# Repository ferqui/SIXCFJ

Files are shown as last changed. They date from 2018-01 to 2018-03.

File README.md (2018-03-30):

# PROJECT SIXCFJ

## Table of Contents
1. [Description](#description)
2. [Requirements](#requirements)
3. [Software Requirements](#software-requirements)
4. [Installation](#installation)
5. [Connections](#connections)
6. [Android/iOS App](#androidios-application)
6. [Mentions](#mentions)
7. [Authors](#credits)

## Description
The objective was the creation of a maze solver using an Arduino Leonardo and some additional sensors. Moreover, once the robot has find the exit, it has to go back to the initial box using the minimal number of steps.

<p align="center">
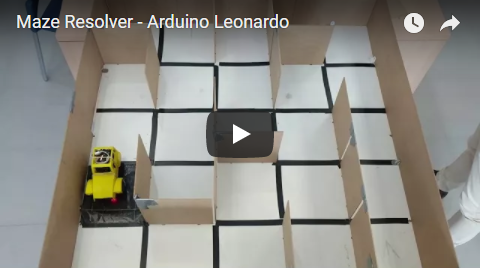
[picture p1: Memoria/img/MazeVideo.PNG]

</p>

## Requirements
* 1 Arduino Leonardo
* 1 Ultrasonic Sensor
* 2 Sharp Infrared Sensor
* 1 Bluetooth Module
* 2 Wheel
* 1 Motor driver
* 2 DC Motors
* 3 CNY70
* 3 LED RGB

## Software Requirements
* Arduino IDE
* React-Native

## Installation
First,

> git clone https://github.com/sixcfj/SIXCFJ.git

Once you have the repo, create a new Arduino project with the codes that are in *Arduino Codes/main*.  Then, you just need to upload it to your Arduino Leonardo and that's all.

## Connections

Pin  | Conection
-----| -----
A0 | CNY70 (Left)
A1 | CNY70 (Right)
A3 | Ultrasonic Sensor
A4 | Sharp Sensor (Right)
A5 | CNY70  (Back)
A6  | % of remaining Battery
A8 | Sharp Sensor (Left)
11 | LED3
12 | LED1
13 | LED2
RX,TX | Bluetooth

## Slides
In the slides directory you can run:

> npm start

This will runs the app in the development mode. Open http://localhost:3000 to view it in the browser.

## Android/iOS Application
First of all, download the dependencies with

> npm start

Then, you need to edit */node_modules/react-native-bluetooth-serial/android/src/main/java/com/rusel/RCTBluetoothSerial/RCTBluetoothSerialPackage* and delete those *__override__*.

Finally, just run one of these commands

> react-native run-android

> react-native run-ios

<p align="center">
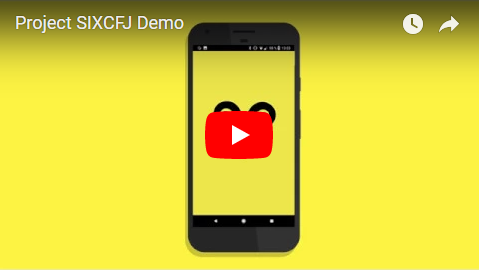
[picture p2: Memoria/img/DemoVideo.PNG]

</p>

About the songs, we can't share them due to copyright issues, but we encourage you to test it with your own music.

## Mentions
We would like to thanks maniacbug for creating this library, it was really helpful for our project. https://github.com/maniacbug/StandardCplusplus .

## Credits
  - Juan Francisco Cabrera Sánchez ([juanfrancs](https://github.com/juanfrancs))
  - Carlos Gallardo Polanco ([gpcarlos](https://github.com/gpcarlos))
  - Fernando Manuel Quintana Velazquez ([ferqui](https://github.com/ferqui))

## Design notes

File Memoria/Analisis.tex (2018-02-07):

\chapter{ANÁLISIS}
\vspace{-20pt}
\section{Casos de uso}

\scalebox{0.8}{
\begin{tikzpicture}
\begin{umlsystem}{Aplicación}
    \umlusecase[x=-3]{Visualizar información}
    \umlusecase[x=0, y=-1]{Conectarse}
    \umlusecase[x=-3,y=-3]{Manejar radiocontrol}
    \umlusecase[x=3,y=-3]{Seleccionar inicio}
\end{umlsystem}

\umlactor[x=-8]{Usuario}
\umlactor[x=8]{Robot}

\umlassoc{Usuario}{usecase-1}
\umlassoc{Usuario}{usecase-2}
\umlassoc{Usuario}{usecase-4}
\umlassoc{Robot}{usecase-2}
\umlassoc{Usuario}{usecase-3}

\end{tikzpicture}
}

\section{Diagrama de flujo}

\begin{figure}[h!]
\centering
\scalebox{0.8}{

\begin{tikzpicture}[node distance=2cm]
  \node (inicio) [startstop] {Inicio};
  \node (detect) [process,below of=inicio] {Detección};
  \node (dcha) [decision,below of=detect,yshift=-0.5cm,xshift=-6.5cm] {\footnotesize ¿Mov Derecha?};
  \node (front) [decision,right of=dcha,xshift=2cm] {\footnotesize ¿Mov Frente?};
  \node (izqda) [decision,right of=front,xshift=2cm] {\footnotesize ¿Mov Izquierda?};
  \node (movDerecha) [process,below of=dcha,yshift=-1cm] {Mov Derecha};
  \node (movFrente) [process,below of=front,yshift=-1cm] {Mov Frente};
  \node (movIzquierda) [process,below of=izqda,yshift=-1cm] {Mov Izquierda};
  \node (movAtras) [process,right of=movIzquierda,xshift=2.5cm] {Deshacer movimiento};
  \node (final) [decision,below of=movFrente,yshift=-1cm,xshift=2cm] {\footnotesize ¿Casilla final?};
  \node (Inv) [process,below of=final,yshift=-1cm] {Camino Inverso};
  \node (null) [right of= movAtras]{\ };

  \draw[arrow] (inicio) -- (detect);
  \draw[arrow] (detect) -| (dcha);
  \draw[arrow] (dcha) -- node[anchor=south]{No} (front);
  \draw[arrow] (front) -- node[anchor=south]{No} (izqda);
  \draw[arrow] (dcha) -- node[anchor=west]{Sí} (movDerecha);
  \draw[arrow] (izqda) -- node[anchor=west]{Sí} (movIzquierda);
  \draw[arrow] (front) -- node[anchor=west]{Sí} (movFrente);
  \draw[arrow] (izqda) -| node[anchor=south]{No}(movAtras);
  \draw[arrow] (movDerecha) -- node[anchor=west]{}(final);
  \draw[arrow] (movIzquierda) -- node[anchor=west]{}(final);
  \draw[arrow] (movFrente) -- node[anchor=west]{}(final);
  \draw[arrow] (movAtras) -- node[anchor=west]{}(final);
  \draw (final.east) -| node[anchor=west]{No} (null.north);
  \draw[arrow] (null) |- (detect.east);
  \draw[arrow] (final) -- node[anchor=west]{Sí}(Inv);
  %\draw[arrow] (final) to[out=-230,in=150] node[anchor=south]{No}(detect);
\end{tikzpicture}
}
\caption{Diagrama de flujo}
\end{figure}

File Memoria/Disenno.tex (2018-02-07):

\chapter{DISEÑO}

\section{Estructura}

Seguidamente puede ver el código principal para la resolucón del laberinto:

\inputminted{arduino}{code/main.ino}

\vspace{-15pt}
\section{Plan de pruebas}
Se ha implementado una pequeña función que nos permite, a partir mediante Bluetooth conocer el estado de los sensores y poder actuar en consecuencia si las mediciones son anormales.

\begin{minted}{cpp}
void testSensors() {
  if (robot.ReadCNY('L'))
    Serial1.println("CNY L Black");
  else
    Serial1.println("CNY L White");
  if (robot.ReadCNY('R'))
    Serial1.println("CNY R Black");
  else
    Serial1.println("CNY R White");
  if (robot.ReadCNY('B'))
    Serial1.println("CNY B Black");
  else
    Serial1.println("CNY B White");
  Serial1.print("Ultrasonic: "); Serial1.println(robot.ReadUltrasonic());
  Serial1.print("Sharp L: "); Serial1.println(robot.ReadSharp('L'));
  Serial1.print("Sharp R: "); Serial1.println(robot.ReadSharp('R'));
}
\end{minted}

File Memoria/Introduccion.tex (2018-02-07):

\chapter{INTRODUCCIÓN}

\section{Objetivo}
El objetivo de esta práctica es la resolución de un laberinto de 5x5 casillas, en el que la posición de las paredes, se desconoce a priori y en el que las casillas tienen un tamaño de 20x20 cm. Además de resolver el laberinto, es decir, llegar a una casilla de salida cuya posición se desconoce. Una vez que se haya encontrado la casilla de salida, volver a la casilla de entrada por el camino más corto posible.

\begin{itemize}
  \item Movimientos: Desplazamiento hacia delante, hacia atrás, giro a la izquierda y giro a la derecha
  \item Detección: Detección de paredes mediante el uso de sensores Sharp y ultrasonidos, y detección de color mediante el uso de sensores CNY70.
  \item Recogida de información: Se recoge información desde los sensores Sharp, CNY70 y el ultrasonidos.
  \item Algoritmo de resolución del laberinto: Se tiene una jerarquía de movimientos, estando en primer lugar, moverse a la derecha, luego al frente y por último a la izquierda. Todos estos movimientos se van guardando en una pila para que según se vaya avanzando en el laberinto en la pila sólo queden los movimientos que permiten alcanzar la casilla final, para que haciendo los movimientos inversos a los que están en la pila, el robot pueda volver a llegar a la casilla inicial por el camino más corto.
  \item Monitorización de información: La monitorización de la información se realiza a través de la aplicación móvil, que muestra la posición del robot en el laberinto junto con el nivel de batería restante, entre otras cosas.

\end{itemize}

\section{Hardware empleado}
En el diseño final se han utilizado los siguientes componentes:

\begin{itemize}
  \item CNY70: Sensor que mide la intensidad de la luz, permitiendo distinguir colores.
  \item Ultrasonidos: Sensor que permite calcular distancias mediante la producción de sonidos y su rebote.
  \item Sharp: Sensor que permite calcular las distancias mediante el uso de un haz de luz.
  \item HC-06 (Bluetooth): Módulo que permite leer y escribir datos mediante el puerto serie.
  \item Motores DC: Elemento mecánico que permite el movimiento.
  \item LED: Elemento electrónico que se ilumina con el paso de la corriente.
  \item Batería: Proporciona una fuente de alimentación externa.
\end{itemize}

\subsection{Arduino Leonardo}

Para ello, se utilizará una placa Arduino Leonardo, un ordenador personal y un móvil. A través del ordenador, se le descargará en la placa el programa para resolver el laberinto, una vez realizada la descarga del programa, se enlaza mediante Bluetooth la placa y un dispositivo móvil, donde se podrá ver la posición del robot en el laberinto y otros datos interesantes como el porcentaje de batería restante.

\subsection{Sensores}
\begin{itemize}
  \item CNY70: Su uso es necesario para comprobar el paso de una casilla a otra así como para comprobar si se ha llegado a la casilla de salida o no.
  \item Sharp: Se usa para detectar la existencia de paredes laterales.
  \item Ultrasonidos: Se usa para detectar la existencia de paredes frontales.
\end{itemize}

\subsection{Actuadores}
\begin{itemize}
  \item Interruptor: El interruptor es necesario para encender la placa.
\end{itemize}

\subsection{Elementos de comunicación}
\begin{itemize}
  \item HC-06: El conector Bluetooth se usa para mandar información a la app móvil para que en ésta se vean el nivel batería y la posición en el laberinto.
\end{itemize}

\subsection{Alimentación}
\begin{itemize}
  \item Batería de 6 pilas AA: Sirve para alimentar la placa.
\end{itemize}

\subsection{Justificación}
Se consideran que estos elementos son los mínimos imprescindibles para una correcta resolución del laberinto, ya que, desde un primer momento, el hecho de buscar un diseño similar al de un coche, teníamos claro que el ultrasonidos iría colocado en el lugar de los faros delanteros y por lo tanto, el uso de los servos resulta totalmente prescindible. Por otra parte, tampoco se usa el conector Bluetooth para el PC por estar utilizando una aplicación móvil.

\subsection{Resumen de Pines}
\begin{table}[h!]
  \centering
  \begin{tabular}{cc}

      \begin{tabular}{|c|c|}
        \hline
        PIN & ELEMENTO \\ \hline
        A5 & CNY Trasero \\ \hline
        A0 & CNY Izquierdo \\ \hline
        A1 & CNY Derecho \\ \hline
        A8 & Sharp Izquierdo \\ \hline
        A4 & Sharp Derecho \\ \hline
        RX, TX & Bluetooth \\ \hline
        A3 & Ultrasonidos \\ \hline
        12 & LED1 \\ \hline
        13 & LED2 \\ \hline
        11 & LED3 \\ \hline
        A6 & \% Batería \\ \hline

      \end{tabular}
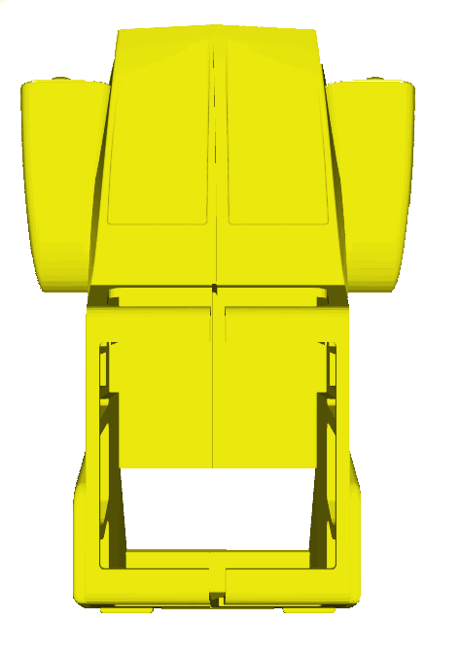
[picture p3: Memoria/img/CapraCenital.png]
    &  \vcenteredhbox{}\\
  \end{tabular}
  \caption{Resumen de los elementos y sus respectivos pines}
  \label{}
\end{table}

\section{Software empleado}
\subsection{Arduino IDE}
Resulta imprescindible el uso de este software por motivos obvios, gracias a él se le mandan los programas a la placa de Arduino. En nuestro caso, era también necesario para importar la librería externa que contiene la implementación de las estructuras de datos de la STL de C++ en Arduino, aunque ésto se detallará más adelante.

\subsection{React-Native}
\textit{React-Native} es una librería de Javascript que permite la creación de aplicaciones que tengan una apariencia nativa en el correspondiente sistema operativo móvil, en este caso en Android y iOS, usando un mismo código. ¿Por qué usar un móvil y no un PC? La respuesta viene dada con dos componentes, el primero la portabilidad y el segundo, la potencia.

Comenzando por la portabilidad, es evidente que es muchísimo más fácil transportar un móvil que un ordenador portátil, de esta forma, ante la posibilidad de tener que hacer presentaciones, sólo haría falta el robot y el móvil, ya que la placa de Arduino poseer una memoria flash, llevaría cargado el programa previamente. En cuanto a la potencia, la realidad es que en los últimos años la tecnología móvil ha avanzado lo suficiente como para igualar en ciertos aspectos al ordenador portátil, por tanto, si tuviesemos que mandar a realizar unos cálculos ya sea al ordenador o al móvil, como por ejemplo, calcular el camino de vuelta más corto usando el algoritmo de Dijkstra no habría tanta diferencia entre que lo haga un móvil o un ordenador.

Y, por otro lado, está el factor didáctico. \textit{React-Native} es una librería con un gran empuje en los últimos años y, de cara a aumentar nuestra formación en otras tecnologías, resultaba bastante interesante aprender lo más actual en el mundo empresarial.

\subsection{\LaTeX}
El hecho de utilizar \LaTeX \ era obligatorio en nuestra opinión para dotar a esta memoria de un aspecto académico, gracias en gran medida al paquete TikZ que permite la creación de gráficos vectoriales en \LaTeX \ con una gran versatilidad. Este paquete permite, por ejemplo, la creación de diagramas de Gantt, de diagramas de casos de uso o de diagramas de flujo.

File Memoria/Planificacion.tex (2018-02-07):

\chapter{PLANIFICACIÓN}

En la primera reunión se decidió que todos colaboraríamos en la codificación del algoritmo del robot y que, además, cada uno de los integrantes del grupo, además de esta tarea, abarcaría otra tarea individual. Esto queda claro en el sistema de colores empleado en diagrama de Gantt que podrá ver en la siguiente página.

\begin{landscape}
\makebox[15pt][c]{
\begin{minipage}{0.21\linewidth}
\begin{ganttchart}[
  hgrid,vgrid, x unit=2mm, time slot format=isodate,newline shortcut=true,
bar label node/.append style=%
{align=center},
bar label font={\footnotesize},
  x unit=0.32cm, canvas/.style={fill=yellow!10,draw=gray,very thick},
  title label font={\tiny}
]{2017-11-25}{2018-2-13}
  \gantttitlecalendar{year,month=name,day} \\
  \ganttbar[bar/.append style={fill=RedOrange!40}]{Códigos\\ sensores}{2017-11-25}{2017-11-30}\\
  \ganttlinkedbar[bar/.append style={fill=RedOrange!40}]{Librería}{2017-11-30}{2018-01-15}\\
  \ganttbar[bar/.append style={fill=Yellow!60}]{Diseño\\ piezas 3D}{2017-12-15}{2018-01-02}\\
  \ganttlinkedbar[bar/.append style={fill=Yellow!60}]{Impresión\\ piezas 3D}{2018-01-02}{2018-01-06}\\
  \ganttlinkedbar[bar/.append style={fill=RedOrange!40}]{Pruebas}{2018-01-06}{2018-01-10}\\
  \ganttlinkedbar[bar/.append style={fill=RedOrange!40}]{Implementación\\ del algoritmo}{2017-12-16}{2018-2-12}\\
  \ganttbar[bar/.append style={fill=LimeGreen!50}]{Aplicación\\móvil}{2017-12-10}{2018-02-12}\\
  \ganttbar[bar/.append style={fill=RoyalBlue!20}]{Documentación}{2017-11-25}{2018-02-06}
\end{ganttchart}
\end{minipage}
}

\

\begin{center}
\crule[LimeGreen!50]{0.5cm}{0.5cm} Fernando \hspace{1cm}
\crule[RoyalBlue!20]{0.5cm}{0.5cm} Juan Francisco \hspace{1cm}
\crule[Yellow!60]{0.5cm}{0.5cm} Carlos \hspace{1cm}
\crule[RedOrange!40]{0.5cm}{0.5cm} Común
\end{center}

\end{landscape}

\restoregeometry

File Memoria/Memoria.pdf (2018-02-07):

# Project SIXCFJ (Robot Móvil)

# https://github.com/ferqui/SIXCFJ

## Juan Francisco Cabrera Sánchez Carlos Gallardo Polanco Fernando Manuel Quintana Velázquez

## 7 de febrero de 2018

# Índice general

1. INTRODUCCIÓN | 5
2. ESPECIFICACIÓN DE REQUISITOS | 8
3. PLANIFICACIÓN | 9
4. PRESUPUESTO | 11
5. ANÁLISIS | 12

6. DISEÑO | 13
7. IMPLEMENTACIÓN | 16
8. MONTAJE | 17
9. PRUEBAS | 20
10. MEJORAS | 21
Apéndices | 22
A. Especificacion del TAD Robot | 23
B. Implementacion del TAD Robot | 24

# Índice de figuras

5.1. Diagrama de flujo | | 12
8.1. Elementos del robot | | 17
8.2. Diseño de las piezas 3D | | 17
8.3. Piezas del Ultrasonidos y los Sharp | | 18
8.4. Imagen del robot con su chásis | | 18
8.5. Galería del robot | | 19
8.6. Muestra de la aplicación móvil | | 19

# Índice de cuadros

# Capítulo 1

# INTRODUCCIÓN

## 1.1. Objetivo

El objetivo de esta práctica es la resolución de un laberinto de 5x5 casillas, en el que la posición de las paredes, se desconoce a priori y en el que las casillas tienen un tamaño de 20x20 cm. Además de resolver el laberinto, es decir, llegar a una casilla de salida cuya posición se desconoce. Una vez que se haya encontrado la casilla de salida, volver a la casilla de entrada por el camino más corto posible.

Movimientos: Desplazamiento hacia delante, hacia atrás, giro a la izquierda y giro a la derecha

Detección: Detección de paredes mediante el uso de sensores Sharp y ultrasonidos, y detección de color mediante el uso de sensores CNY70.

Recogida de información: Se recoge información desde los sensores Sharp, CNY70 y el ultrasonidos.

Algoritmo de resolución del laberinto: Se tiene una jerarquía de movimientos, estando en primer lugar, moverse a la derecha, luego al frente y por último a la izquierda. Todos estos movimientos se van guardando en una pila para que según se vaya avanzando en el laberinto en la pila sólo queden los movimientos que permiten alcanzar la casilla final, para que haciendo los movimientos inversos a los que están en la pila, el robot pueda volver a llegar a la casilla inicial por el camino más corto.

Monitorización de información: La monitorización de la información se realiza a través de la aplicación móvil, que muestra la posición del robot en el laberinto junto con el nivel de batería restante, entre otras cosas.

## 1.2. Hardware empleado

## En el diseño final se han utilizado los siguientes componentes:

CNY70: Sensor que mide la intensidad de la luz, permitiendo distinguir colores.

Ultrasonidos: Sensor que permite calcular distancias mediante la producción de sonidos y su rebote.

Sharp: Sensor que permite calcular las distancias mediante el uso de un haz de luz.

HC-06 (Bluetooth): Módulo que permite leer y escribir datos mediante el puerto serie.

Motores DC: Elemento mecánico que permite el movimiento.

LED: Elemento electrónico que se ilumina con el paso de la corriente.

Batería: Proporciona una fuente de alimentación externa.

## 1.2.1. Arduino Leonardo

Para ello, se utilizará una placa Arduino Leonardo, un ordenador personal y un móvil. A través del ordenador, se le descargará en la placa el programa para resolver el laberinto, una vez realizada la descarga del programa, se enlaza mediante Bluetooth la placa y un dispositivo móvil, donde se podrá ver la posición del robot en el laberinto y otros datos interesantes como el porcentaje de batería restante.

## 1.2.2. Sensores

CNY70: Su uso es necesario para comprobar el paso de una casilla a otra así como para comprobar si se ha llegado a la casilla de salida o no.

Sharp: Se usa para detectar la existencia de paredes laterales.

Ultrasonidos: Se usa para detectar la existencia de paredes frontales.

## 1.2.3. Actuadores

Interruptor: El interruptor es necesario para encender la placa.

## 1.2.4. Elementos de comunicación

HC-06: El conector Bluetooth se usa para mandar información a la app móvil para que en ésta se vean el nivel batería y la posición en el laberinto.

## 1.2.5. Alimentación

Batería de 6 pilas AA: Sirve para alimentar la placa.

## 1.2.6. Justificación

Se consideran que estos elementos son los mínimos imprescindibles para una correcta resolución del laberinto, ya que, desde un primer momento, el hecho de buscar un diseño similar al de un coche, teníamos claro que el ultrasonidos iría colocado en el lugar de los faros delanteros y por lo tanto, el uso de los servos resulta totalmente prescindible. Por otra parte, tampoco se usa el conector Bluetooth para el PC por estar utilizando una aplicación móvil.

## 1.2.7. Resumen de Pines

PIN | ELEMENTO

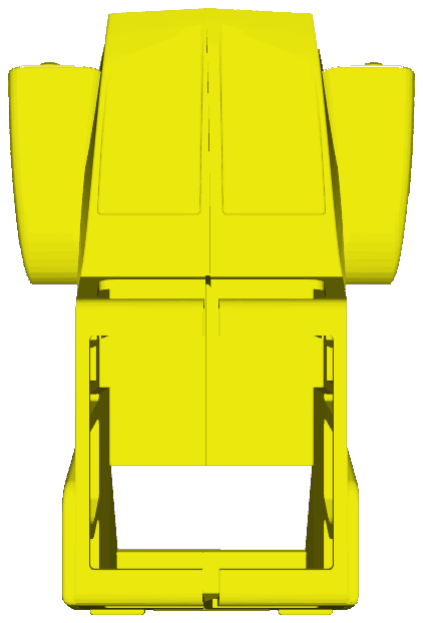
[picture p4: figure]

A5 | CNY Trasero
A0 | CNY Izquierdo
A1 | CNY Derecho
A8 | Sharp Izquierdo
A4 | Sharp Derecho
RX, TX | Bluetooth
A3 | Ultrasonidos
12 | LED1
13 | LED2
11 | LED3
A6 | % Batería

## Cuadro 1.1: Resumen de los elementos y sus respectivos pines

## 1.3. Software empleado

## 1.3.1. Arduino IDE

Resulta imprescindible el uso de este software por motivos obvios, gracias a él se le mandan los programas a la placa de Arduino. En nuestro caso, era también necesario para importar la librería externa que contiene la implementación de las estructuras de datos de la STL de C++ en Arduino, aunque ésto se detallará más adelante.

## 1.3.2. React-Native

React-Native es una librería de Javascript que permite la creación de aplicaciones que tengan una apariencia nativa en el correspondiente sistema operativo móvil, en este caso en Android y iOS, usando un mismo código. ¿Por qué usar un móvil y no un PC? La respuesta viene dada con dos componentes, el primero la portabilidad y el segundo, la potencia.
Comenzando por la portabilidad, es evidente que es muchísimo más fácil transportar un móvil que un ordenador portátil, de esta forma, ante la posibilidad de tener que hacer presentaciones, sólo haría falta el robot y el móvil, ya que la placa de Arduino poseer una memoria flash, llevaría cargado el programa previamente. En cuanto a la potencia, la realidad es que en los últimos años la tecnología móvil ha avanzado lo suficiente como para igualar en ciertos aspectos al ordenador portátil, por tanto, si tuviesemos que mandar a realizar unos cálculos ya sea al ordenador o al móvil, como por ejemplo, calcular el camino de vuelta más corto usando el algoritmo de Dijkstra no habría tanta diferencia entre que lo haga un móvil o un ordenador.
Y, por otro lado, está el factor didáctico. React-Native es una librería con un gran empuje en los últimos años y, de cara a aumentar nuestra formación en otras tecnologías, resultaba bastante interesante aprender lo más actual en el mundo empresarial.

## 1.3.3. LATEX

El hecho de utilizar LATEX era obligatorio en nuestra opinión para dotar a esta memoria de un aspecto académico, gracias en gran medida al paquete TikZ que permite la creación de gráficos vecto-riales en LATEX con una gran versatilidad. Este paquete permite, por ejemplo, la creación de diagramas de Gantt, de diagramas de casos de uso o de diagramas de flujo.

# Capítulo 2

# ESPECIFICACIÓN DE REQUISITOS

## 2.1. Requisitos funcionales

ID | CATEGORÍA | DESCRIPCIÓN
RF01 | Movimiento | El robot debe ser capaz de moverse
RF02 | Movimiento | El robot debe ser capaz de pivotar 90º a derecha
RF03 | Movimiento | El robot debe ser capaz de pivotar 90º a izquierda
RF04 | Movimiento | El robot debe ser capaz de avanzar en línea recta
RF05 | Movimiento | El robot avanza adecuadamente hasta la siguiente celda
RF06 | Detección | El robot debe ser capaz de detectar una pared frontal
RF07 | Detección | El robot debe ser capaz de detectar una pared lateral derecha
RF08 | Detección | El robot debe ser capaz de detectar una pared lateral izquierda
RF09 | Detección | El robot debe ser capaz de detectar la transición entre celdas
RF10 | Detección | El robot debe ser capaz de detectar la celda de salida
RF11 | Resolución | El robot almacena información sobre las celdas del laberinto
RF12 | Resolución | El robot es capaz de decidir el siguiente movimiento en base a la información sobre la celda
RF13 | Resolución | El robot es capaz de recorrer varias celdas del laberinto siguiendo el algoritmo empleado
RF14 | Resolución | El robot es capaz de salir del laberinto
RF15 | Información | El robot envía al PC información sobre el número de celdas recorridas
RF16 | Información | El robot envía al PC información sobre obstáculos en cada celda
RF17 | Información | El robot envía al PC información sobre la velocidad de movimiento
RF18 | Información | El robot envía al PC información sobre la distancia recorrida
RF19 | Información | El robot envía al PC información sobre el tiempo transcurrido desde la entrada al laberinto
RF20 | Información | El robot envía al PC sobre la trayectoria ejecutada
RF21 | Información | El robot envía al PC información sobre el número de celdas recorridas
RF22 | Información | El PC muestra una representación gráfica del laberinto
RF23 | Usuario | Interfaz gráfica en PC que recopile información
RF24 | Pruebas | Incluir modo test al arranque del robot

## Cuadro 2.1: Requisitos Funcionales

## 2.2. Requisitos no funcionales

ID | CATEGORÍA | DESCRIPCIÓN | ACCIÓN
RNF01 | Tamaño | Condicionado por las dimensiones del laberinto <Casilla de 20cm x 20cm; Laberinto de 1m x 1m>
RNF02 | Consumo | Condicionado por la batería disponible <6 pilas AA >
RNF03 | Errores | El robot choca contra una pared | -
RNF04 | Errores | Batería a punto de agotarse | Sustituir batería
RNF05 | Errores | El robot gira continuamente | No se produce
RNF06 | Errores | El robot sobrepasa 20 minutos sin conseguir salir | -

## Cuadro 2.2: Requisitos no Funcionales

# Capítulo 3

# PLANIFICACIÓN

En la primera reunión se decidió que todos colaboraríamos en la codificación del algoritmo del robot y que, además, cada uno de los integrantes del grupo, además de esta tarea, abarcaría otra tarea individual. Esto queda claro en el sistema de colores empleado en diagrama de Gantt que podrá ver en la siguiente página.

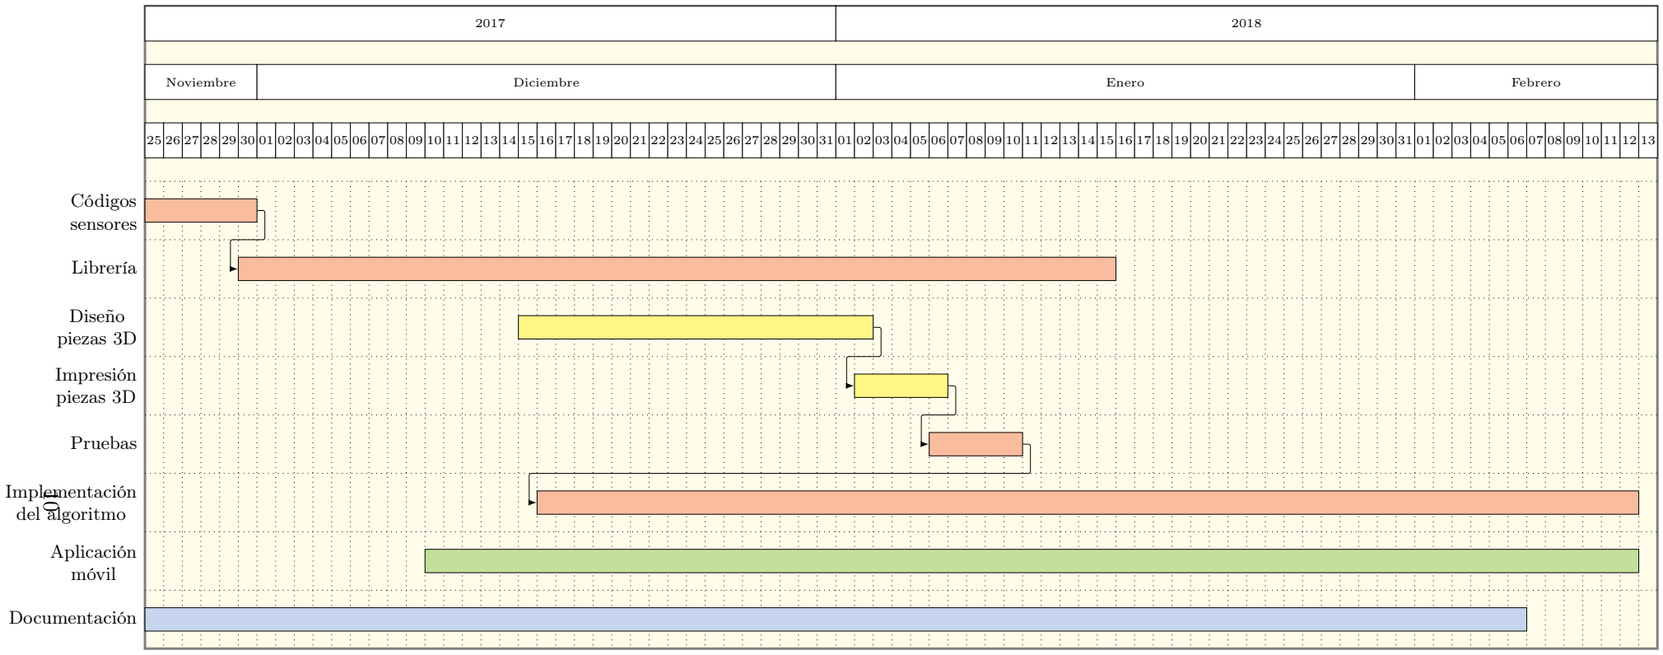
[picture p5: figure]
Noviembre; Diciembre; Enero; Febrero; Códigos sensores; Librería; Diseño piezas 3D; Impresión piezas 3D; Pruebas; Implementación del algoritmo; Aplicación móvil; Documentación

25 26 27 28 29 30 01 02 03 04 05 06 07 08 09 10 11 12 13 14 15 16 17 18 19 20 21 22 23 24 25 26 27 28 29 30 31 01 02 03 04 05 06 07 08 09 10 11 12 13 14 15 16 17 18 19 20 21 22 23 24 25 26 27 28 29 30 31 01 02 03 04 05 06 07 08 09 10 11 12 13

Fernando | Juan Francisco | Carlos | Común

# Capítulo 4

# PRESUPUESTO

Producto | Nº de unidades | Precio/Unidad | Precio Total
Arduino Leonardo | 1 | 18e | 18e
Shield | 1 | 30e | 30e
CNY70 | 3 | 1.15e | 3.45e
HC-06 | 1 | 3.50e | 3.50e
Sharp | 2 | 3.30e | 6.60e
Ultrasonidos | 1 | 1e | 1e
Batería | 1 | 1.65e | 1.65e
Bovina PLA | 150g | 150g * 0.02e | 3e
Rendimiento de la impresora 3D | 0.150kW/h | 0.150kW/h* 24h * 0.145ekW/h | 0.52e
Mano de Obra | 100h | 17e | 1700e
| | | Total: 1767.72e

## Cuadro 4.1: Presupuesto del Robot Móvil

# Capítulo 5

# ANÁLISIS

## 5.1. Casos de uso

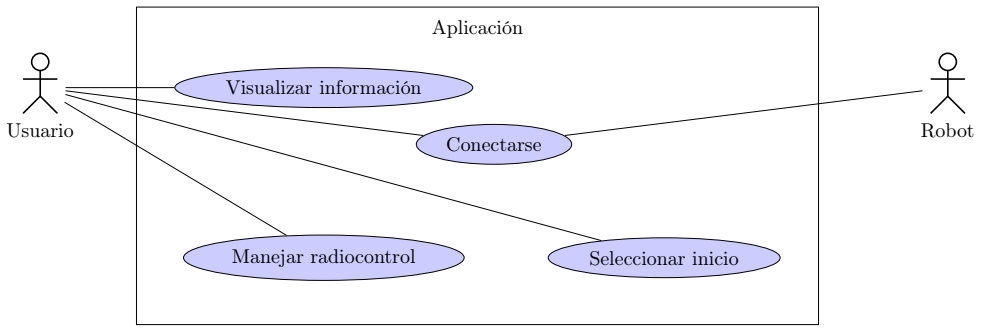
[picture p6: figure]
Aplicación; Visualizar información; Conectarse; Manejar radiocontrol; Seleccionar inicio; Usuario; Robot

## 5.2. Diagrama de flujo

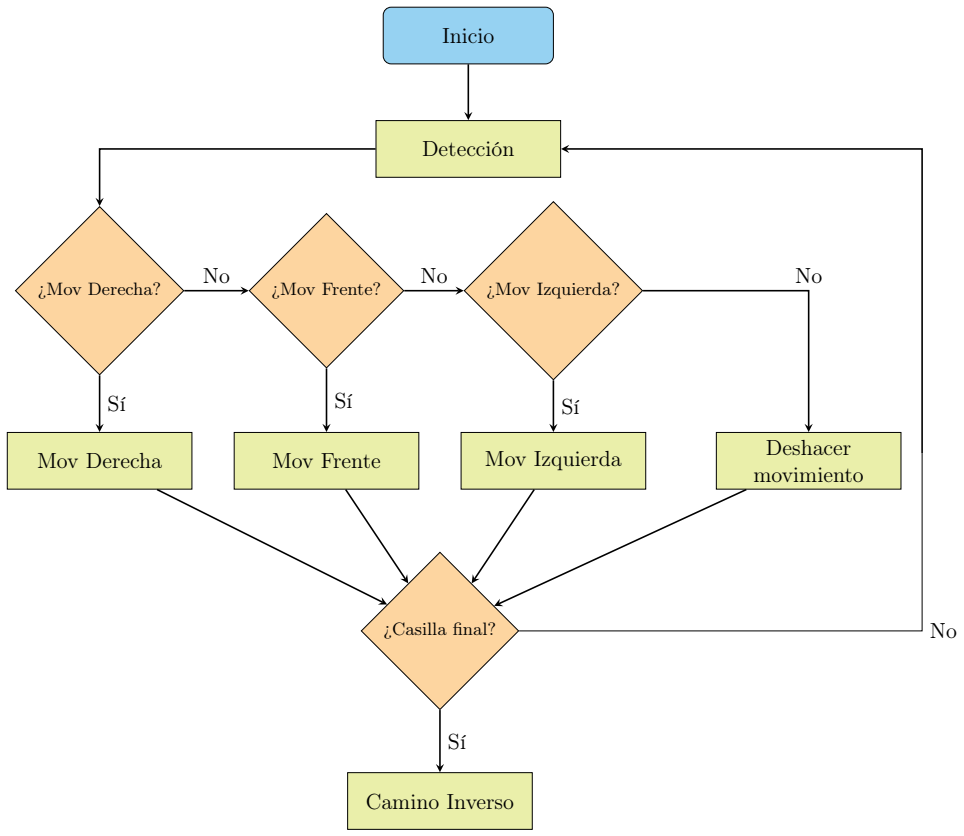
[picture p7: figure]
Inicio; Detección; ¿Mov Derecha?; ¿Mov Frente?; ¿Mov Izquierda?; Mov Derecha; Mov Frente; Mov Izquierda; Deshacer; movimiento; ¿Casilla final?; Camino Inverso

## Figura 5.1: Diagrama de flujo

# Capítulo 6

# DISEÑO

## 6.1. Estructura

## Seguidamente puede ver el código principal para la resolucón del laberinto:

#include <StandardCplusplus.h>

#include <stack>

#include "Timer.h"

#include "Robot.hpp"

const int RIGHT = 1;
const int FORWARD = 2;
const int LEFT = 4;
const int BACKWARD = 8;
const int LEFT_BACKWARD = 16; const int RIGHT_BACKWARD = 32;

Timer t;

int lastMovement = 0;
std::stack<int> Movements;

int CNY[] = {A0,A1,A5}; // CNYLeft, CNYRight, CNYBottom int Sharp[] = {A8,A4}; // SHarpLeft, SharpRight
int Ultrasonic = A3;
int MotorR[] = {5,6};
int MotorL[] = {9,10};
int Led[] = {12,13,11}; // Led1, Led2, Led3
int Battery = A6;

Robot::tState State = Robot::lookingforEXIT; // Must start in waiting

Robot robot(CNY,Sharp,Ultrasonic,MotorL,MotorR,Led,Battery,State,3,2);

void handle_battery(){
//Serial1.print("bt" + String(pos[0]) + String(pos[1])+"#"); Serial1.print("bt" + String(robot.BatteryState(),2) + "#"); }

void setup() {
Serial1.begin(9600); // Bluetooth Serial.begin(9600);
robot.init();
int tickEvent = t.every(500, handle_battery); }

void loop() {
delay(10000);
switch (State) {
case Robot::waiting:

break;

case Robot::lookingforEXIT: lookforEXIT();
break;

case Robot::lookingforSTART:

break;
}
}

void lookforEXIT() {
while (!isTheEnd()) {
int allowedMovement = checkWalls(); if (allowedMovement & RIGHT) {
robot.Move(Robot::right,200); robot.Move(Robot::forward,200); robot.Move(Robot::stoprobot,0); testSensors(); //delay(5000); } else {
if (allowedMovement & FORWARD) { robot.Move(Robot::forward,200); robot.Move(Robot::stoprobot,0); testSensors(); //delay(5000); } else {
if (allowedMovement & LEFT) {
robot.Move(Robot::left,200);
robot.Move(Robot::forward,200); robot.Move(Robot::stoprobot,0); testSensors(); //delay(5000); } else {
robot.Move(Robot::turn_back,200); robot.Move(Robot::stoprobot,0); testSensors(); //delay(5000); }
}
}
}
robot.Move(Robot::stoprobot,0); }

void lookforSTART() {

}

int checkWalls() {
int result = 0;
if (12 < robot.ReadSharp('L') || robot.ReadSharp('L') < 0) { result |= LEFT;
}
if (12 < robot.ReadSharp('R') || robot.ReadSharp('R') < 0) { result |= RIGHT;
}
if (5 < robot.ReadUltrasonic()) {
result |= FORWARD;
}
return result;
}

void radioControl(String m) { robot.Encoder(false);
//if (Serial1.available() > 0 ) { //String m = robot.ReadBT(); robot.MoveAbsolute(m[0],150,150); //}
}

bool isTheEnd() { // All CNY are Black return robot.ReadCNY('L')&&robot.ReadCNY('R')&&robot.ReadCNY('B'); }

void testSensors() {
if (robot.ReadCNY('L'))
Serial1.println("CNY L Black"); else Serial1.println("CNY L White"); if (robot.ReadCNY('R'))
Serial1.println("CNY R Black"); else Serial1.println("CNY R White"); if (robot.ReadCNY('B'))
Serial1.println("CNY B Black");
else Serial1.println("CNY B White");
Serial1.print("Ultrasonic: "); Serial1.println(robot.ReadUltrasonic()); Serial1.print("Sharp L: "); Serial1.println(robot.ReadSharp('L')); Serial1.print("Sharp R: "); Serial1.println(robot.ReadSharp('R'));
}

## 6.2. Plan de pruebas

Se ha implementado una pequeña función que nos permite, a partir mediante Bluetooth conocer el estado de los sensores y poder actuar en consecuencia si las mediciones son anormales.

void testSensors() {
if (robot.ReadCNY('L'))
Serial1.println("CNY L Black"); else
Serial1.println("CNY L White"); if (robot.ReadCNY('R'))
Serial1.println("CNY R Black"); else
Serial1.println("CNY R White"); if (robot.ReadCNY('B'))
Serial1.println("CNY B Black");
else
Serial1.println("CNY B White");
Serial1.print("Ultrasonic: "); Serial1.println(robot.ReadUltrasonic()); Serial1.print("Sharp L: "); Serial1.println(robot.ReadSharp('L')); Serial1.print("Sharp R: "); Serial1.println(robot.ReadSharp('R'));
}

# Capítulo 7

# IMPLEMENTACIÓN

## 7.1. Librerías

## 7.1.1. Librería Externa

Se intentó utilizar en un primer lugar la STL de C++, pero no se pudo utilizar tal, por tanto,

## buscamos alternativas y acabamos encontrando un repositorio de Github 1 en el que se habían imple-

mentado todas las estructuras de la STL en Arduino. Ésto nos permitió utilizar una de las ideas que habíamos barajado inicialmente, que era la reducción de caminos para la vuelta atrás, que, además, tenía como ventaja con respecto a utilizar uno de los algoritmos clásicos como Floyd o Dijkstra, un menor coste computacional.

## 7.1.2. Librería Propia

Se ha implementado una librería en la que haciendo uso del paradigma de la Programación Orien-tada a Objetos, se permite utilizar un objeto de la clase Robot para acceder a todas las funciones de la clase. Para ver la implementación tanto de la especificación como de la implementación, diríjase a los Apéndices A y B.

## 7.2. Apuntes sobre el código

Para hacer un código más legible y mantenible durante el desarrollo del TAD Robot se ha optado por separar la codificación en dos archivos, un primer archivo en el que se encuentren las cabeceras de las funciones, Robot.hpp, y otro segundo archivo en el que se encuentran las implementaciones del TAD.
Por otro lado, se hacen uso de las interrupciones y de los encoders para dotar de una mayor precisión a los giros, aunque existe el problema de las dimensiones del laberinto, que dificulta en ocasiones la resolución del laberinto al haber utilizado un chasis que recubre la placa.
El funcionamiento general del mismo consiste en, inicialmente hacer una detección del entorno. A partir de ésta, se decide cuál es el próximo movimiento a realizar, que se guardará posteriormente en una pila. Supongamos que el robot ha girado a la derecha y se encuentra una pared frontal. Se desharía este movimiento y como anteriormente ha realizado un giro a la derecha, ahora sólo tendría dos posibles movimientos, moverse hacia adelante o girar a la izquierda. De esta forma se consigue que el robot consiga llegar a la casilla final, con una pila que contiene el número mínimo de movimientos.

1https://github.com/maniacbug/StandardCplusplus

# Capítulo 8

# MONTAJE

Se le ofrece a continuación de estas líneas, un diagrama de bloques en el que se pueden apreciar los distintos componentes que se han utilizado y cómo se conectan entre sí.

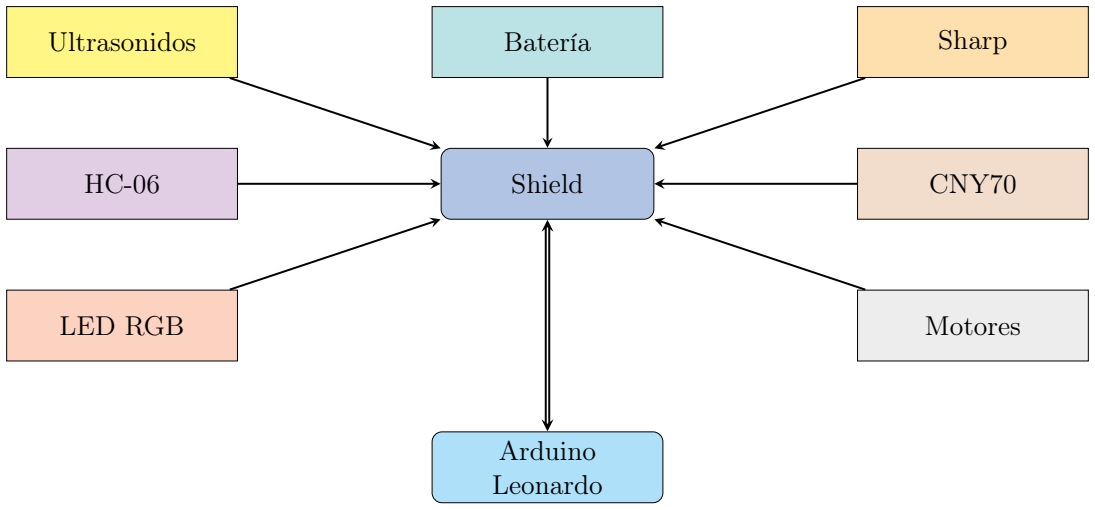
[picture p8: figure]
Shield; CNY70; Sharp; Ultrasonidos; LED RGB; Motores; Batería; Arduino Leonardo

## Figura 8.1: Elementos del robot

Antes de mostrar el resultado final, nos gustaría mostrar el proceso seguido hasta llegar a la versión final del robot. Se muestra en primer lugar el diseño de las piezas 3D, con la mejora del uso de soportes en formas de árbol, para que no hubiese ningún problema durante la impresión.

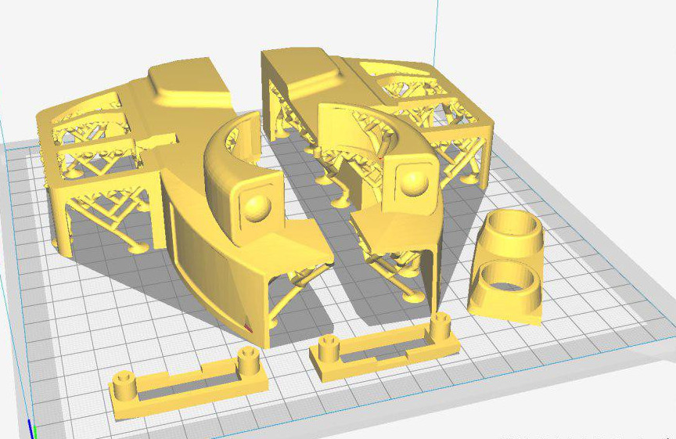
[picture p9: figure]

## Figura 8.2: Diseño de las piezas 3D

Se observa a continuación el resultado de las piezas impresas para el ultrasonidos y los sharp.

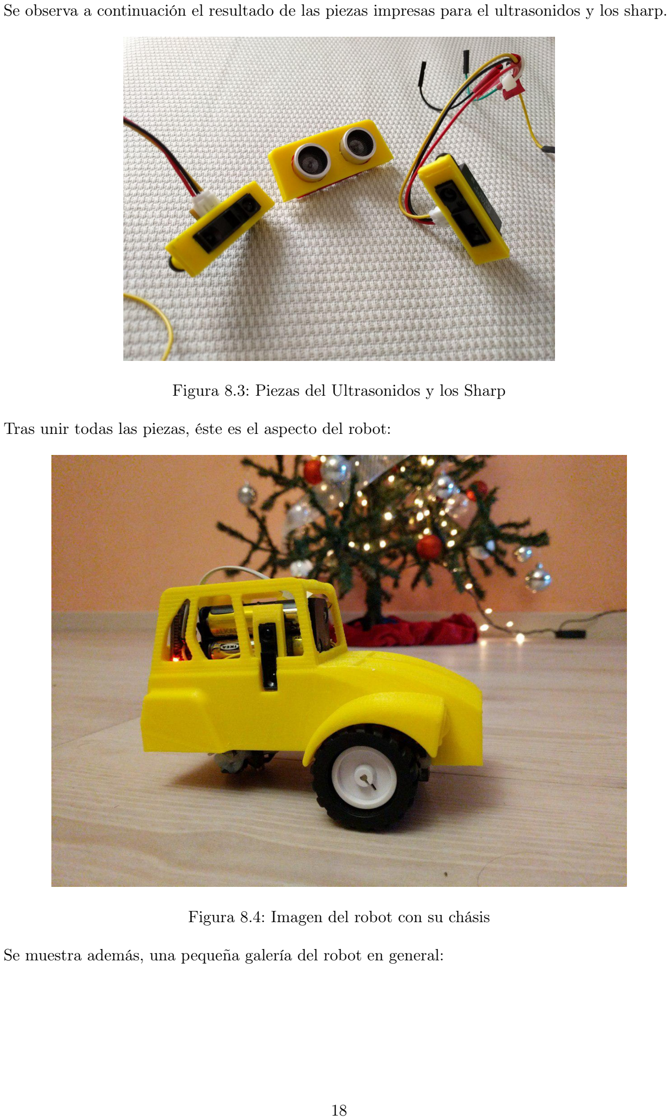
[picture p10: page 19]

## Figura 8.3: Piezas del Ultrasonidos y los Sharp

## Tras unir todas las piezas, éste es el aspecto del robot:

## Figura 8.4: Imagen del robot con su chásis

## Se muestra además, una pequeña galería del robot en general:

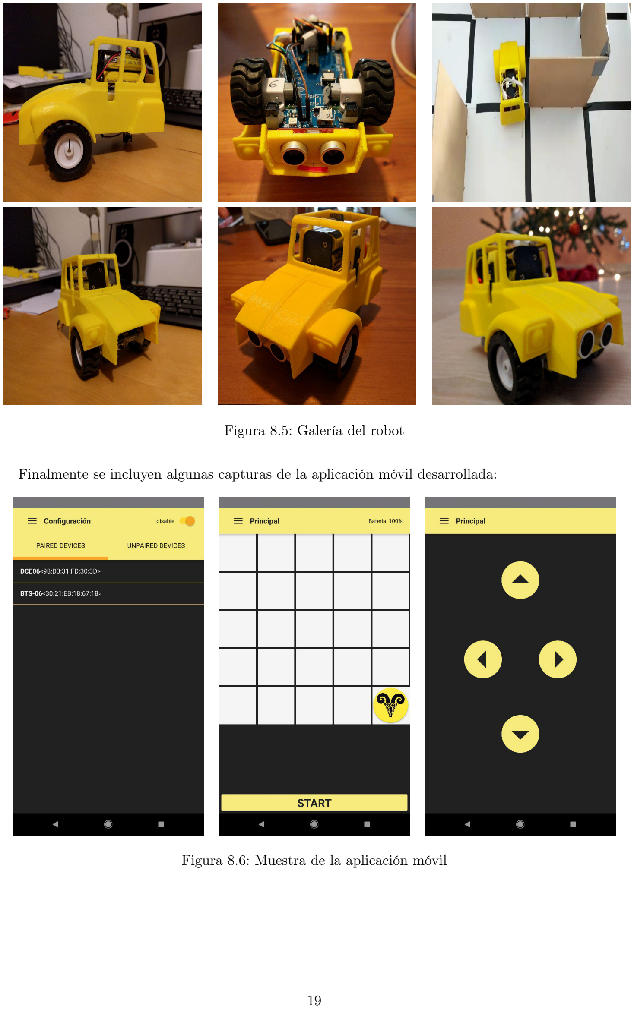
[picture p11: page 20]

## Figura 8.5: Galería del robot

## Finalmente se incluyen algunas capturas de la aplicación móvil desarrollada:

## Figura 8.6: Muestra de la aplicación móvil

# Capítulo 9

# PRUEBAS

ID | CATEGORÍA | COMPROBACIÓN
RF01 | Movimiento | El robot se mueve gracias al uso de los encoders.
RF02 | Movimiento | El robot es capaz de girar 90º a la derecha con uso de encoders.
RF03 | Movimiento | El robot es capaz de girar 90º a la izquierda con el uso de encoders.
RF04 | Movimiento | El robot al no detectar una pared frontal, es capaz de moverse en línea recta.
RF05 | Movimiento | Al cumplirse el requisito anterior, se cumple este.
RF06 | Detección | Gracias al uso de ultrasonidos, se detecta la existencia de paredes frontales.
RF07 | Detección | Gracias al uso del Sharp derecho, se detecta la existencia de paredes a la derecha.
RF08 | Detección | Gracias al uso del Sharp izquierdo, se detecta la existencia de paredes a la derecha.
RF09 | Detección | Gracias al uso de los CNY70 se detecta la transición entre celdas.
RF10 | Detección | Gracias al uso de los CNY70 se detecta la casilla de salida.
RF11 | Resolución | Se almacena información sobre las celdas ya visitadas.
RF12 | Resolución | Debido al RF anterior, se decide cuáles son los posibles movimientos a realizar.
RF13 | Resolución | El robot es capaz de recorrer varias celdas gracias al algoritmo implementado.
RF14 | Resolución | El robot es capaz de resolver el laberinto.
RF15 | Información | Se manda información a la app sobre las celdas recorridas.
RF16 | Información | Se manda información a la app sobre sobre los obstáculos que hay en cada celda.
RF17 | Información | Se manda información a la app sobre la velocidad que lleva el robot.
RF18 | Información | Se manda información a la app sobre la distancia que ha recorrido el robot.
RF19 | Información | Se manda información a la app sobre el tiempo que lleva el robot en el laberinto.
RF20 | Información | Se manda información sobre la trayectoria realizada por el robot.
RF21 | Información | Se manda información sobre el nº de celdas recorridas.
RF22 | Información | La aplicación muestra el estado del laberinto, tal y como se muestra en la figura 8.4
RF23 | Usuario | El usuario dispone de una aplicación móvil en la que puede comprobar multitud de cosas
RF24 | Pruebas | Se dispone de una batería de pruebas que comprueba el correcto funcionamiento de todos los sensores

## Cuadro 9.1: Requisitos Funcionales

# Capítulo 10

# MEJORAS

La principal y mayor mejora, además del diseño de las piezas 3D, es la aplicación desarrollada para las plataformas de Android e iOS. Esta aplicación permite ir más allá de la simple lectura del puerto Serial del Arduino y es que, es posible, controlar visualmente el estado del robot en el laberinto en cada momento, y además, el control de los movimientos que puede realizar el robot. Se incluyen además, algunas mejoras audiovisuales, como es el uso de la luz y de los sonidos para indicar los distintos eventos que pueden ocurrir.

# Apéndices

# Apéndice A

# Especificacion del TAD Robot

#ifndef ROBOT_H

#define ROBOT_H

#include "Arduino.h"

class Robot {

public:
enum tState {waiting, lookingforEXIT, lookingforSTART};
enum tMove1 {forward, backward, right, left, rightbackward, leftbackward, turn_back, ,→ stoprobot};
enum tMove2 {E_forward, E_backward, E_right, E_left, E_rightbackward, E_leftbackward};

Robot(int* CNY, int* Sharp, int Ultrasonic, int* MotorL, int* MotorR,
| int* Led, int Battery, tState State, int left_encoder, int right_encoder): CNY{CNY}, Sharp{Sharp}, Ultrasonic{Ultrasonic}, MotorL{MotorL}, MotorR{MotorR}, Led{Led}, Battery{Battery}, State{State}, left_encoder{left_encoder}, right_encoder{right_encoder} {};

void init();

void Move(Robot::tMove1, int speed);
void MoveEncoder(Robot::tMove2, int speedL, int speedR, float nT); void MoveAbsolute(char direction, int speedL, int speedR);
void TurnOnLed(char color, int intensity);
bool ReadCNY(char CNY);
float ReadSharp(char sharp);
float ReadUltrasonic();
void WriteBT();
String ReadBT();
void set_State(tState s) {State=s;} tState get_State() {return State;} float BatteryState();
void Encoder(bool state);

~Robot();

private :
int* CNY; // CNYLeft, CNYRight, CNYBottom int* Sharp; // SHarpLeft, SharpRight
int Ultrasonic;
int* MotorR;
int* MotorL;
int* Led; // Led1, Led2, Led3 int Battery;
int left_encoder;
int right_encoder;
tState State;

};

#endif

# Apéndice B

# Implementacion del TAD Robot

#include "Robot.hpp"

volatile float nTicks = 0;

volatile unsigned long leftCount = 0; volatile unsigned long rightCount = 0;

int* LEFT;
int* RIGHT;
bool EncoderState = true;

void Robot::Encoder(bool state){ EncoderState = state;
}

void right_handle() {
if (RIGHT != NULL && EncoderState) { if (rightCount >= nTicks) { analogWrite(RIGHT[0],LOW); analogWrite(RIGHT[1],LOW);
}
++rightCount;
}
}

void left_handle() {
if (LEFT != NULL && EncoderState) { if (leftCount >= nTicks) { analogWrite(LEFT[0],LOW);
analogWrite(LEFT[1],LOW);
}
++leftCount;
}
}

void Robot::init() {
LEFT = MotorL;
RIGHT = MotorR;
pinMode(MotorL[0], OUTPUT); pinMode(MotorL[1], OUTPUT); pinMode(MotorR[0], OUTPUT); pinMode(MotorR[1], OUTPUT); pinMode(Led[0], OUTPUT);
pinMode(Led[1], OUTPUT);
pinMode(Led[2], OUTPUT);
pinMode(left_encoder, INPUT);
pinMode(right_encoder, INPUT);

attachInterrupt(digitalPinToInterrupt(left_encoder), left_handle, RISING); attachInterrupt(digitalPinToInterrupt(right_encoder), right_handle, RISING); }

void Robot::Move(Robot::tMove1 mov, int speed) { const float difference = 0.75;
rightCount=0;
leftCount=0;
switch (mov) {
case Robot::forward: // Forward EncoderState = false;
while (!ReadCNY('B')) {
int basura = ReadUltrasonic();
if (ReadSharp('L') < 12 && ReadSharp('R') < 12) { // Two Walls if (ReadSharp('L')-ReadSharp('R') < -2) { MoveAbsolute('f',speed,speed*difference);
} else {
if (ReadSharp('L')-ReadSharp('R') > 2) { MoveAbsolute('f',speed*difference,speed); } else {
MoveAbsolute('f',speed,speed);
}
}
} else {
if (ReadSharp('L') < 12 && ReadSharp('R') > 12 && ReadSharp('R') < 20) { // Left Wall if (ReadSharp('L') < 4) {
MoveAbsolute('f',speed,speed*difference);
} else {
if (ReadSharp('L') > 8) {
MoveAbsolute('f',speed*difference,speed); } else {
MoveAbsolute('f',speed,speed);
}
}
} else {
if (ReadSharp('L') > 12 && ReadSharp('L') < 20 && ReadSharp('R') < 12) { // Right Wall if (ReadSharp('R') < 4) {
MoveAbsolute('f',speed*difference,speed);
} else {
if (ReadSharp('R') > 8) {
MoveAbsolute('f',speed,speed*difference); } else {
MoveAbsolute('f',speed,speed);
}
}
} else { // Now Walls
MoveAbsolute('f',speed,speed); }
}
}
}
while (!ReadCNY('R') && !ReadCNY('L') && !(ReadUltrasonic()>2 && ReadUltrasonic()<3)) { Serial1.println(ReadUltrasonic());
if (ReadSharp('L') < 12 && ReadSharp('R') < 12) { // Two Walls
if (ReadSharp('L')-ReadSharp('R') < -2) { MoveAbsolute('f',speed,speed*difference);
} else {
if (ReadSharp('L')-ReadSharp('R') > 2) { MoveAbsolute('f',speed*difference,speed); } else {
MoveAbsolute('f',speed,speed);
}
}
} else {
if (ReadSharp('L') < 12 && ReadSharp('R') > 12 && ReadSharp('R') < 20) { // Left Wall if (ReadSharp('L') < 4) {
MoveAbsolute('f',speed,speed*difference);
} else {
if (ReadSharp('L') > 8) {
MoveAbsolute('f',speed*difference,speed);

} else {
MoveAbsolute('f',speed,speed); }
}
} else {
if (ReadSharp('L') > 12 && ReadSharp('L') < 20 && ReadSharp('R') < 12) { // Right Wall if (ReadSharp('R') < 4) {
MoveAbsolute('f',speed*difference,speed);
} else {
if (ReadSharp('R') > 8) {
MoveAbsolute('f',speed,speed*difference); } else {
MoveAbsolute('f',speed,speed);
}
}
} else { // Now Walls
MoveAbsolute('f',speed,speed); }
}
}
}
EncoderState = true;
MoveEncoder(Robot::E_backward,speed,speed,2); break;

case Robot::backward: // Backward
EncoderState = false;
while (!ReadCNY('R') && !ReadCNY('L')) {
if (ReadSharp('L') < 12 && ReadSharp('R') < 12) { // Two Walls if (ReadSharp('L')-ReadSharp('R') < -2) { MoveAbsolute('b',speed,speed*difference);
} else {
if (ReadSharp('L')-ReadSharp('R') > 2) { MoveAbsolute('b',speed*difference,speed); } else {
MoveAbsolute('b',speed,speed);
}
}
} else {
if (ReadSharp('L') < 12 && ReadSharp('R') > 12 && ReadSharp('R') < 20) { // Left Wall if (ReadSharp('L') < 4) {
MoveAbsolute('b',speed,speed*difference);
} else {
if (ReadSharp('L') > 6) {
MoveAbsolute('b',speed*difference,speed); } else {
MoveAbsolute('b',speed,speed);
}
}
} else {
if (ReadSharp('L') > 12 && ReadSharp('L') < 20 && ReadSharp('R') < 12) { // Right Wall if (ReadSharp('R') < 4) {
MoveAbsolute('b',speed*difference,speed);
} else {
if (ReadSharp('R') > 6) {
MoveAbsolute('b',speed,speed*difference); } else {
MoveAbsolute('b',speed,speed);
}
}
} else { // Now Walls
MoveAbsolute('b',speed,speed); }
}
}
}

while (!ReadCNY('B')) {
if (ReadSharp('L') < 12 && ReadSharp('R') < 12) { // Two Walls if (ReadSharp('L')-ReadSharp('R') < -2) { MoveAbsolute('b',speed,speed*difference);
} else {
if (ReadSharp('L')-ReadSharp('R') > 2) { MoveAbsolute('b',speed*difference,speed); } else {
MoveAbsolute('b',speed,speed);
}
}
} else {
if (ReadSharp('L') < 12 && ReadSharp('R') > 12 && ReadSharp('R') < 20) { // Left Wall if (ReadSharp('L') < 4) {
MoveAbsolute('b',speed,speed*difference);
} else {
if (ReadSharp('L') > 6) {
MoveAbsolute('b',speed*difference,speed); } else {
MoveAbsolute('b',speed,speed);
}
}
} else {
if (ReadSharp('L') > 12 && ReadSharp('L') < 20 && ReadSharp('R') < 12) { // Right Wall if (ReadSharp('R') < 4) {
MoveAbsolute('b',speed*difference,speed);
} else {
if (ReadSharp('R') > 6) {
MoveAbsolute('b',speed,speed*difference); } else {
MoveAbsolute('b',speed,speed);
}
}
} else { // Now Walls
MoveAbsolute('b',speed,speed); }
}
}
}
EncoderState = true;
rightCount=0; leftCount=0; MoveEncoder(Robot::E_forward,speed,speed,2); break;

case Robot::left: // Left
MoveEncoder(Robot::E_leftbackward,speed,speed,2); MoveEncoder(Robot::E_backward,speed,speed,2); MoveEncoder(Robot::E_rightbackward,speed,speed,2); MoveEncoder(Robot::E_left,speed,speed,12);
break;

case Robot::right: // Right MoveEncoder(Robot::E_rightbackward,speed,speed,2); MoveEncoder(Robot::E_backward,speed,speed,2); MoveEncoder(Robot::E_leftbackward,speed,speed,2); MoveEncoder(Robot::E_right,speed,speed,12); break;

case Robot::leftbackward: // Left MoveEncoder(Robot::E_leftbackward,speed,speed,2); MoveEncoder(Robot::E_forward,speed,speed,3); MoveEncoder(Robot::E_rightbackward,speed,speed,2); MoveEncoder(Robot::E_leftbackward,speed,speed,12); break;

case Robot::rightbackward: // Right

MoveEncoder(Robot::E_rightbackward,speed,speed,2); MoveEncoder(Robot::E_forward,speed,speed,3); MoveEncoder(Robot::E_leftbackward,speed,speed,2); MoveEncoder(Robot::E_rightbackward,speed,speed,12); break;

case Robot::turn_back:
MoveEncoder(Robot::E_rightbackward,speed,speed,3); MoveEncoder(Robot::E_backward,speed,speed,4); MoveEncoder(Robot::E_leftbackward,speed,speed,3); MoveEncoder(Robot::E_forward,speed,speed,4); rightCount=0; leftCount=0; nTicks = 10; analogWrite(MotorR[0],speed); analogWrite(MotorR[1],LOW); analogWrite(MotorL[0],LOW); analogWrite(MotorL[1],speed);
while((rightCount < nTicks) || (leftCount < nTicks)){} break;

default: // Stop
analogWrite(MotorR[0],LOW); analogWrite(MotorR[1],LOW); analogWrite(MotorL[0],LOW); analogWrite(MotorL[1],LOW); }
}

void Robot::MoveEncoder(Robot::tMove2 mov, int speedL, int speedR, float nT) { nTicks = nT;
rightCount=0;
leftCount=0;
switch (mov) {
case Robot::E_forward:
analogWrite(MotorR[0],LOW); analogWrite(MotorR[1],speedR); analogWrite(MotorL[0],LOW); analogWrite(MotorL[1],speedL);
while((rightCount < nTicks) || (leftCount < nTicks)){} break;

case Robot::E_backward: // Back analogWrite(MotorR[0],speedR); analogWrite(MotorR[1],LOW); analogWrite(MotorL[0],speedL); analogWrite(MotorL[1],LOW);
while((rightCount < nTicks) || (leftCount < nTicks)){} break;

case Robot::E_right:
analogWrite(MotorR[0],LOW); analogWrite(MotorR[1],LOW); analogWrite(MotorL[0],LOW); analogWrite(MotorL[1],speedL); while(leftCount < nTicks){} break;

case Robot::E_left:
analogWrite(MotorR[0],LOW); analogWrite(MotorR[1],speedR); analogWrite(MotorL[0],LOW); analogWrite(MotorL[1],LOW); while(rightCount < nTicks){} break;

case Robot::E_rightbackward: analogWrite(MotorR[0],LOW);

analogWrite(MotorR[1],LOW); analogWrite(MotorL[0],speedL); analogWrite(MotorL[1],LOW); while(leftCount < nTicks){} break;

case Robot::E_leftbackward: analogWrite(MotorR[0],speedR); analogWrite(MotorR[1],LOW); analogWrite(MotorL[0],LOW); analogWrite(MotorL[1],LOW); while(rightCount < nTicks){} break;

default: // Stop
analogWrite(MotorR[0],LOW); analogWrite(MotorR[1],LOW); analogWrite(MotorL[0],LOW); analogWrite(MotorL[1],LOW); }
}

void Robot::MoveAbsolute(char position, int speedL, int speedR) { switch (position) {
case 'f': // Forward
analogWrite(MotorR[0],LOW);
analogWrite(MotorR[1],speedR); analogWrite(MotorL[0],LOW); analogWrite(MotorL[1],speedL); break;

case 'b': // Back
analogWrite(MotorR[0],speedR); analogWrite(MotorR[1],LOW); analogWrite(MotorL[0],speedL); analogWrite(MotorL[1],LOW); break;

case 'l': // Left
analogWrite(MotorR[0],LOW); analogWrite(MotorR[1],speedR); analogWrite(MotorL[0],speedL); analogWrite(MotorL[1],LOW); break;

case 'r': // Right
analogWrite(MotorR[0],speedR); analogWrite(MotorR[1],LOW); analogWrite(MotorL[0],LOW); analogWrite(MotorL[1],speedL); break;

default: // Stop
analogWrite(MotorR[0],LOW); analogWrite(MotorR[1],LOW); analogWrite(MotorL[0],LOW); analogWrite(MotorL[1],LOW); }

}

void Robot::TurnOnLed(char color, int intensity) { switch (color) {
case 'R' : analogWrite(Led[0],intensity); break; case 'G' : analogWrite(Led[1],intensity); break;

case 'B' : analogWrite(Led[2],intensity); break; default:
analogWrite(Led[0],0);
analogWrite(Led[1],0);
analogWrite(Led[2],0);
}
}

bool Robot::ReadCNY(char cny) { int limit = 700;
int value;
switch (cny){
case 'L': value = analogRead(CNY[0]); break; case 'R': value = analogRead(CNY[1]); break; case 'B': value = analogRead(CNY[2]); break; default: value = 0;
}
//Serial1.print(value);
if (value>limit)
return true; // Black
else
return false; // White
}

float Robot::ReadSharp(char sharp) {
const float ResolutionADC = 0.00488, /*4.88mV*/ b = 0.024, m = 11.89;
int Value_Sharp = 0;
switch (sharp){
case 'L': Value_Sharp = analogRead(Sharp[0]); break; case 'R': Value_Sharp = analogRead(Sharp[1]); break; default: Value_Sharp = 0;
}
float Voltage = Value_Sharp*ResolutionADC;
float x = (Voltage-b)/m;
return (1-0.42*x)/x;
}

float Robot::ReadUltrasonic() { float distance;
unsigned long time_bounce;

pinMode(Ultrasonic,OUTPUT); digitalWrite(Ultrasonic,LOW); delayMicroseconds(5);
digitalWrite(Ultrasonic,HIGH); delayMicroseconds(10);
digitalWrite(Ultrasonic,LOW); pinMode(Ultrasonic,INPUT);
time_bounce = pulseIn(Ultrasonic,HIGH); distance = 0.017 * time_bounce;

return distance;
}

String Robot::ReadBT() {
String s = Serial1.readStringUntil('#'); Serial1.read();
return s;
}

float Robot::BatteryState() {
return analogRead(Battery)*(5.00/1023.00)*2+0.7; }

Robot::~Robot(){}

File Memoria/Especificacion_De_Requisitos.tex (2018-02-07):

\chapter{ESPECIFICACIÓN DE REQUISITOS}

\vspace{-20pt}
\section{Requisitos funcionales}

\begin{center}
\begin{table}[h!]
  \begin{adjustbox}{max width=\textwidth}
  \begin{tabular}{|c|c|c|}
    \hline
    ID & CATEGORÍA & DESCRIPCIÓN \\ \hline
    \rowcolor{gray!20}

    RF01 & Movimiento & El robot debe ser capaz de moverse  \\ \hline
    \rowcolor{gray!20}

    RF02 & Movimiento & El robot debe ser capaz de pivotar 90º a derecha \\ \hline
    \rowcolor{gray!20}

    RF03 & Movimiento & El robot debe ser capaz de pivotar 90º a izquierda \\ \hline
    \rowcolor{gray!20}

    RF04 & Movimiento & El robot debe ser capaz de avanzar en línea recta \\ \hline
    \rowcolor{gray!20}

    RF05 & Movimiento & El robot avanza adecuadamente hasta la siguiente celda  \\ \hline
    \rowcolor{red!20}

    RF06 & Detección & El robot debe ser capaz de detectar una pared frontal    \\ \hline
    \rowcolor{red!20}

    RF07 & Detección & El robot debe ser capaz de detectar una pared lateral derecha \\ \hline
    \rowcolor{red!20}

    RF08 & Detección & El robot debe ser capaz de detectar una pared lateral izquierda \\ \hline
    \rowcolor{red!20}

    RF09 & Detección  & El robot debe ser capaz de detectar la transición entre celdas \\ \hline
    \rowcolor{red!20}

    RF10 & Detección & El robot debe ser capaz de detectar la celda de salida \\ \hline
    \rowcolor{red!20}

    RF11 & Resolución & El robot almacena información sobre las celdas del laberinto \\ \hline
    \rowcolor{yellow!40}

    RF12 & Resolución & El robot es capaz de decidir el siguiente movimiento en base a la información sobre la celda \\ \hline
    \rowcolor{yellow!40}

    RF13 & Resolución & El robot es capaz de recorrer varias celdas del laberinto siguiendo el algoritmo empleado \\ \hline
    \rowcolor{yellow!40}

    RF14 & Resolución & El robot es capaz de salir del laberinto \\ \hline
    \rowcolor{green!20}

    RF15 & Información & El robot envía al PC información sobre el número de celdas recorridas \\ \hline

    \rowcolor{green!20}

    RF16 & Información & El robot envía al PC información sobre obstáculos en cada celda \\ \hline

    \rowcolor{green!20}

    RF17 & Información & El robot envía al PC información sobre la velocidad de movimiento \\ \hline

    \rowcolor{green!20}

    RF18 & Información & El robot envía al PC información sobre la distancia recorrida \\ \hline

    \rowcolor{green!20}

    RF19 & Información & El robot envía al PC información sobre el tiempo transcurrido desde la entrada al laberinto \\ \hline

    \rowcolor{green!20}

    RF20 & Información & El robot envía al PC sobre la trayectoria ejecutada  \\ \hline

    \rowcolor{green!20}

    RF21 & Información & El robot envía al PC información sobre el número de celdas recorridas \\ \hline

    \rowcolor{green!20}

    RF22 & Información & El PC muestra una representación gráfica del laberinto  \\ \hline
    \rowcolor{orange!40}

    RF23 & Usuario & Interfaz gráfica en PC que recopile información \\ \hline

    \rowcolor{blue!20}

    RF24 & Pruebas & Incluir modo test al arranque del robot \\ \hline

  \end{tabular}
\end{adjustbox}
  \caption{Requisitos Funcionales}
  \label{ReqFuncionales}

\end{table}
\end{center}

\vspace{-20pt}
\section{Requisitos no funcionales}
\begin{center}
\begin{table}[h!]
  \begin{adjustbox}{max width=\textwidth}
  \begin{tabular}{|c|c|c|c|}
    \hline
    ID & CATEGORÍA & DESCRIPCIÓN & ACCIÓN \\ \hline
    \rowcolor{blue!20}

    RNF01 & Tamaño & Condicionado por las dimensiones del laberinto $<$Casilla de 20cm x 20cm; Laberinto de 1m x 1m$>$ &   \\ \hline
    \rowcolor{green!40}

    RNF02 & Consumo & Condicionado por la batería disponible $<$6 pilas AA $>$ &  \\ \hline
    \rowcolor{red!25}

    RNF03 & Errores & El robot choca contra una pared & - \\ \hline
    \rowcolor{red!25}

    RNF04 & Errores & Batería a punto de agotarse & Sustituir batería \\ \hline
    \rowcolor{red!25}

    RNF05 & Errores & El robot gira continuamente & No se produce \\ \hline
    \rowcolor{red!25}

    RNF06 & Errores & El robot sobrepasa 20 minutos sin conseguir salir & - \\ \hline

  \end{tabular}
\end{adjustbox}
  \caption{Requisitos no Funcionales}
  \label{ReqNoFuncionales}

\end{table}
\end{center}

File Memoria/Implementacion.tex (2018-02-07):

\chapter{IMPLEMENTACIÓN}

\section{Librerías}
\subsection{Librería Externa}
Se intentó utilizar en un primer lugar la STL de C++, pero no se pudo utilizar tal, por tanto, buscamos alternativas y acabamos encontrando un repositorio de Github \footnote{https://github.com/maniacbug/StandardCplusplus} en el que se habían implementado todas las estructuras de la STL en Arduino. Ésto nos permitió utilizar una de las ideas que habíamos barajado inicialmente, que era la reducción de caminos para la vuelta atrás, que, además, tenía como ventaja con respecto a utilizar uno de los algoritmos clásicos como Floyd o Dijkstra, un menor coste computacional.

\subsection{Librería Propia}
Se ha implementado una librería en la que haciendo uso del paradigma de la Programación Orientada a Objetos, se permite utilizar un objeto de la clase Robot para acceder a todas las funciones de la clase. Para ver la implementación tanto de la especificación como de la implementación, diríjase a los Apéndices A y B.

\section{Apuntes sobre el código}

Para hacer un código más legible y mantenible durante el desarrollo del TAD Robot se ha optado por separar la codificación en dos archivos, un primer archivo en el que se encuentren las cabeceras de las funciones, \textit{Robot.hpp}, y otro segundo archivo en el que se encuentran las implementaciones del TAD.

Por otro lado, se hacen uso de las interrupciones y de los encoders para dotar de una mayor precisión a los giros, aunque existe el problema de las dimensiones del laberinto, que dificulta en ocasiones la resolución del laberinto al haber utilizado un chasis que recubre la placa.

El funcionamiento general del mismo consiste en, inicialmente hacer una detección del entorno. A partir de ésta, se decide cuál es el próximo movimiento a realizar, que se guardará posteriormente en una pila. Supongamos que el robot ha girado a la derecha y se encuentra una pared frontal. Se desharía este movimiento y como anteriormente ha realizado un giro a la derecha, ahora sólo tendría dos posibles movimientos, moverse hacia adelante o girar a la izquierda. De esta forma se consigue que el robot consiga llegar a la casilla final, con una pila que contiene el número mínimo de movimientos.

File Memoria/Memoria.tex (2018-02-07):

\documentclass[a4paper,11pt,spanish]{report}
\usepackage{style}

\title{Project SIXCFJ (Robot Móvil)\\\url{https://github.com/ferqui/SIXCFJ}}
\author{Juan Francisco Cabrera Sánchez\\ Carlos Gallardo Polanco\\ Fernando Manuel Quintana Velázquez}
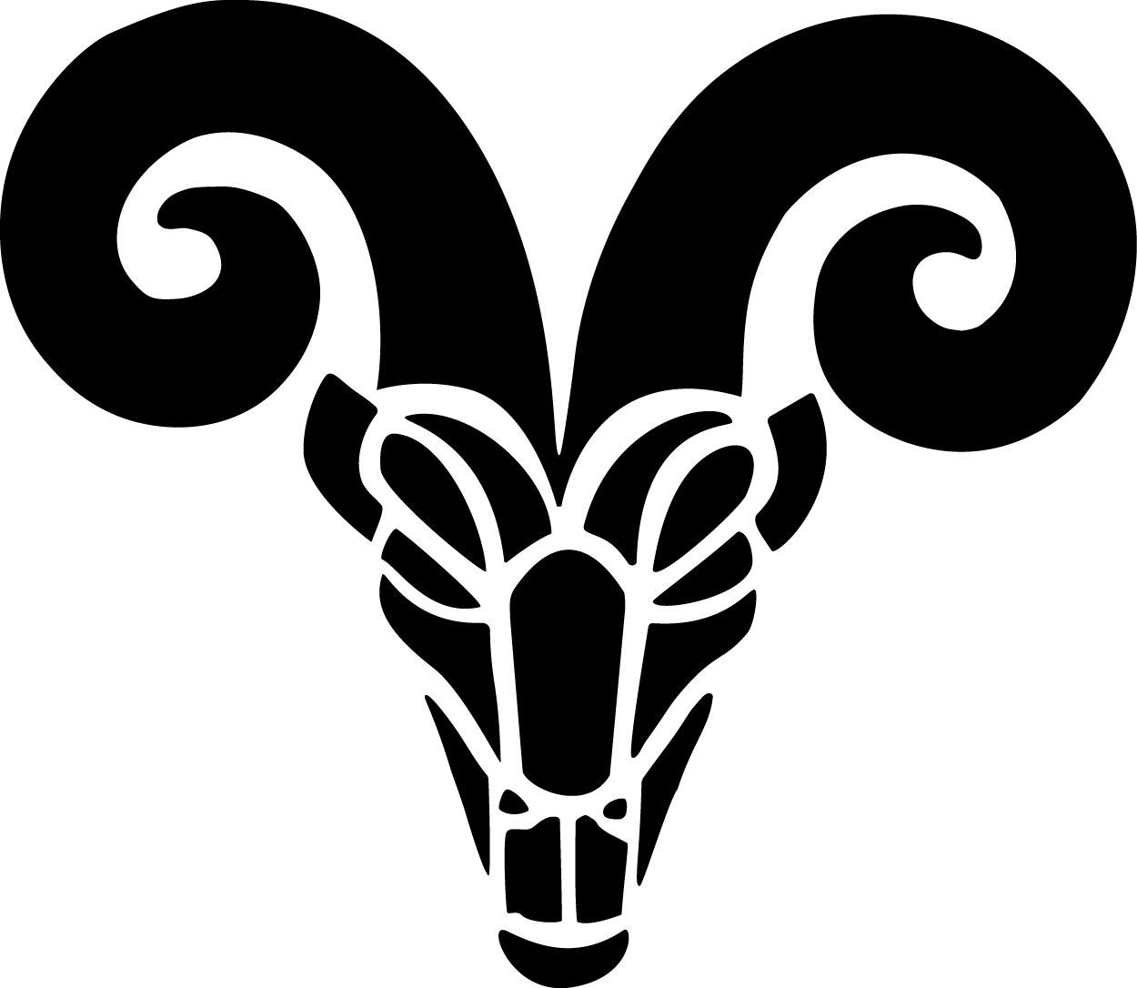
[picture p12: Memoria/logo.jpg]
\date{\today\\ \vspace{25pt} }

\begin{document}

\maketitle

\doublespacing
\tableofcontents
\singlespacing
\listoffigures

\listoftables

\input{Introduccion.tex}

\input{Especificacion_De_Requisitos.tex}

\input{Planificacion.tex}

\input{Presupuesto.tex}

\input{Analisis.tex}

\input{Disenno.tex}

\input{Implementacion.tex}

\input{Montaje.tex}

\input{Pruebas.tex}

\input{Mejoras.tex}

\input{Apendices.tex}

\end{document}

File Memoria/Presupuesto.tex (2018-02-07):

\chapter{PRESUPUESTO}

\begin{center}
\begin{table}[h!]
  \centering
  \begin{tabular}{|c|c|c|c|}
  \hline
  Producto & Nº de unidades & Precio/Unidad & Precio Total \\ \hline
  \hline
  Arduino Leonardo & 1 & 18\euro & 18\euro\\  \hline
  Shield & 1 & 30\euro & 30\euro \\ \hline
  CNY70 & 3 & 1.15\euro &  3.45\euro \\ \hline
  HC-06 & 1 & 3.50\euro & 3.50\euro\\ \hline
  Sharp & 2 & 3.30\euro & 6.60\euro \\ \hline
  Ultrasonidos & 1 & 1\euro & 1\euro \\ \hline
  Batería & 1 & 1.65\euro & 1.65\euro \\ \hline
  Bovina PLA & 150g & 150g * 0.02\euro & 3\euro\\ \hline
  Rendimiento de la impresora 3D & 0.150kW/h & 0.150kW/h* 24h * 0.145\euro kW/h & 0.52\euro \\ \hline
  Mano de Obra & 100h & 17\euro & 1700\euro \\ \hline
  & & & Total: 1767.72\euro \\ \hline
  \end{tabular}
  \caption{Presupuesto del Robot Móvil}
  \label{Presupuesto}

\end{table}
\end{center}

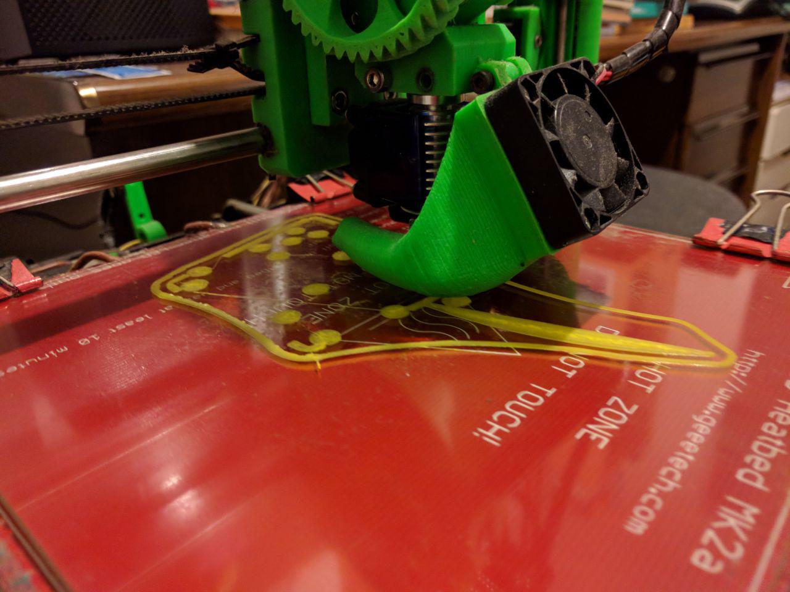
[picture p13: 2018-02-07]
Memoria/img/Caprito3.jpg

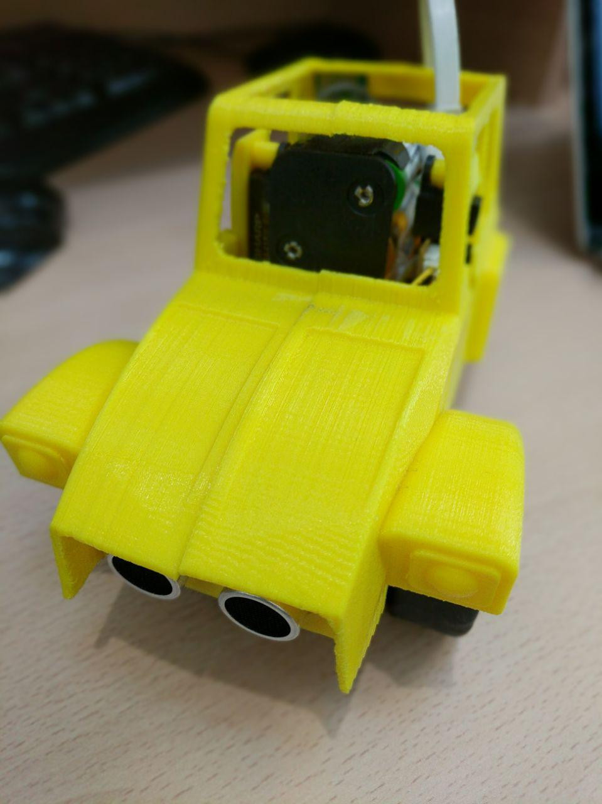
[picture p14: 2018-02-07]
Memoria/img/DCE3.jpg

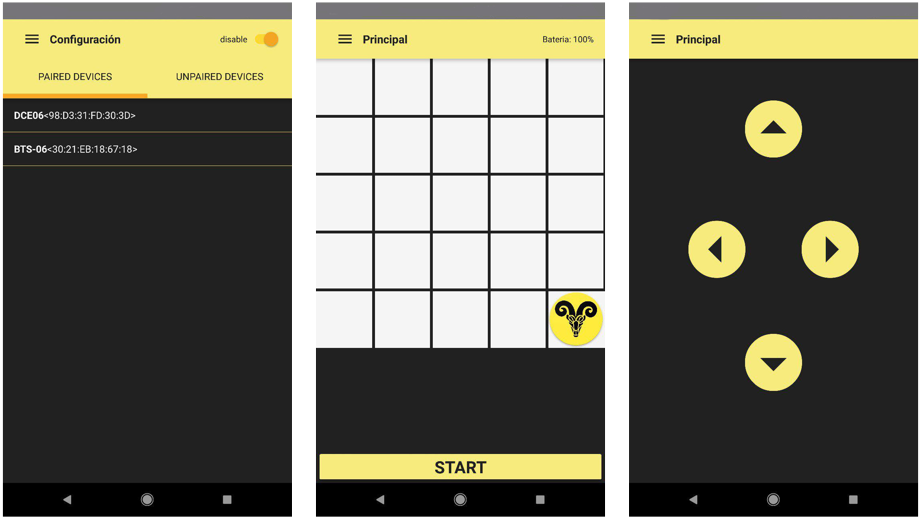
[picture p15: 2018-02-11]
App_git.png

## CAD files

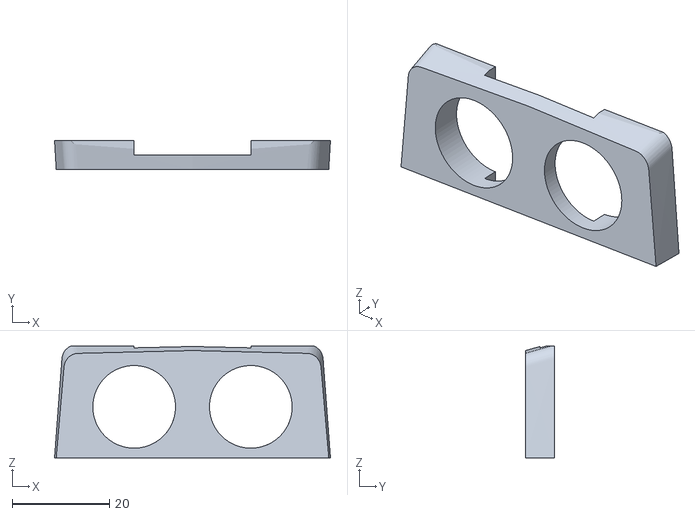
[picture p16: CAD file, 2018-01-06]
3D Model/STL/Ultrasonic.stl
56.8 x 6.00 x 23.0

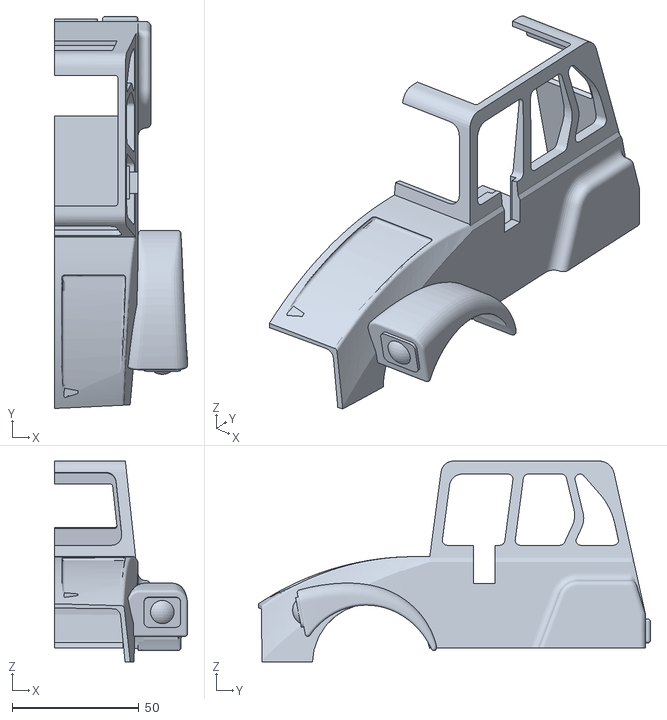
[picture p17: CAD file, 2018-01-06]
3D Model/STL/MitadCocheParte1.stl
52.4 x 154.5 x 79.2

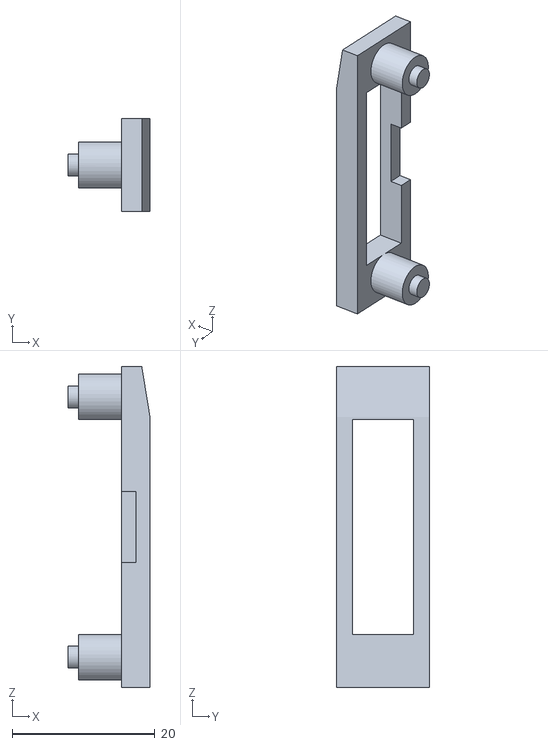
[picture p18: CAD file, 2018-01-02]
3D Model/STL/Sharp.stl
11.5 x 13.0 x 45.0

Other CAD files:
3D Model/STL/MitadCocheParte2.stl

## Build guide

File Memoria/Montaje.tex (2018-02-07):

\chapter{MONTAJE}
Se le ofrece a continuación de estas líneas, un diagrama de bloques en el que se pueden apreciar los distintos componentes que se han utilizado y cómo se conectan entre sí.
\begin{figure}[h!]
\centering
\begin{tikzpicture}[node distance=4cm]
  \node (Shield) [Shield,draw] at(0,0) {Shield};
  \node (CNY70) [CNY70, draw] at (6,0){CNY70};
  \node (Sharp) [Sharp, draw] at (6,2) {Sharp};
  \node (HC-06) [HC-06, draw] at (-6,0){HC-06};
  \node (Ultrasonido) [Ultrasonido, draw] at(-6,2) {Ultrasonidos};
  \node (LED RGB) [RGB, draw] at (-6,-2){LED RGB};
  \node (Motores) [Motores, draw] at (6,-2) {Motores};
  \node (Bateria) [Bateria, draw] at (0,2) {Batería};
  \node (ArduinoLeonardo) [ArduinoLeonardo, draw] at (0,-4) {Arduino Leonardo};

  \draw[arrow] (CNY70)--(Shield);
  \draw[arrow] (Sharp)--(Shield);
  \draw[arrow] (HC-06)--(Shield);
  \draw[arrow] (LED RGB)--(Shield);
  \draw[arrow] (Motores)--(Shield);
  \draw[arrow] (Ultrasonido)--(Shield);
  \draw[arrow] (Bateria)--(Shield);
  \draw[darrow] (Shield)--(ArduinoLeonardo);

\end{tikzpicture}
\caption{Elementos del robot}
\end{figure}

Antes de mostrar el resultado final, nos gustaría mostrar el proceso seguido hasta llegar a la versión final del robot. Se muestra en primer lugar el diseño de las piezas 3D, con la mejora del uso de soportes en formas de árbol, para que no hubiese ningún problema durante la impresión.

\begin{figure}[h!]
  \centering
  
  \caption{Diseño de las piezas 3D}
  \label{B}
\end{figure}

\

\

Se observa a continuación el resultado de las piezas impresas para el ultrasonidos y los sharp.

\begin{figure}[h!]
  \centering
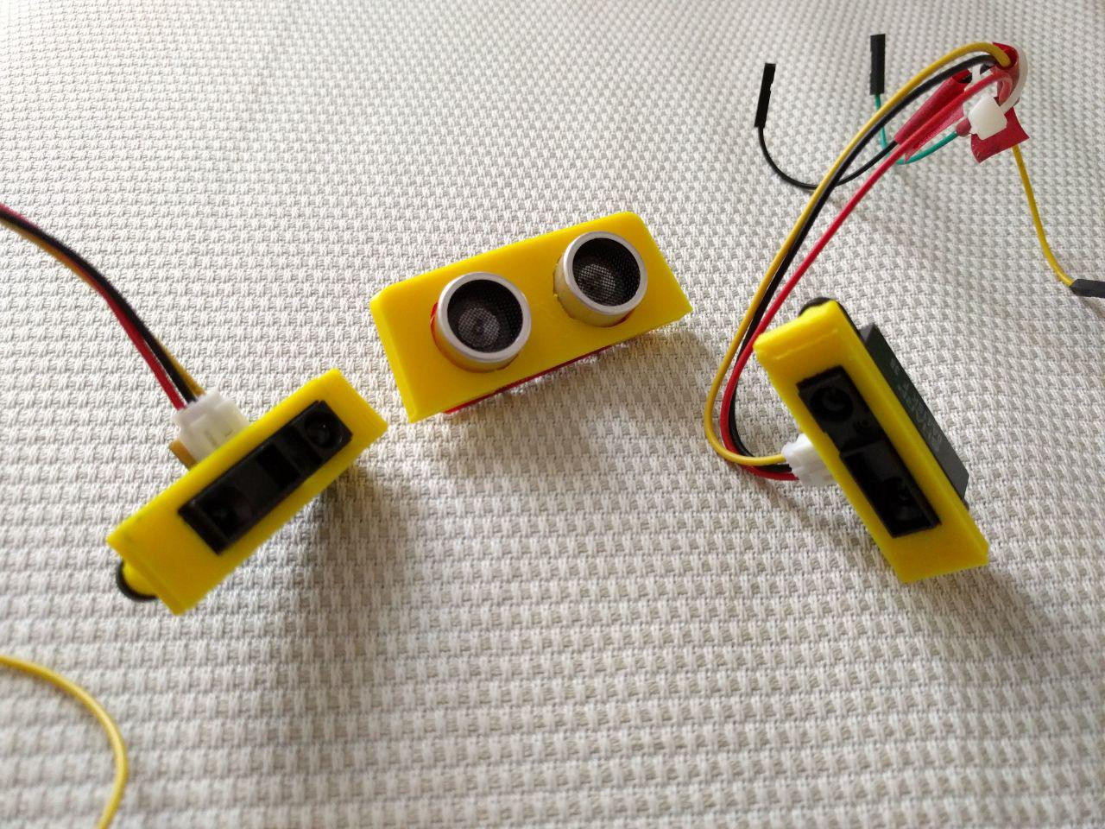
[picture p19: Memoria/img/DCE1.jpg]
  
  \caption{Piezas del Ultrasonidos y los Sharp}
  \label{A}
\end{figure}

Tras unir todas las piezas, éste es el aspecto del robot:

\begin{figure}[h!]
  \centering
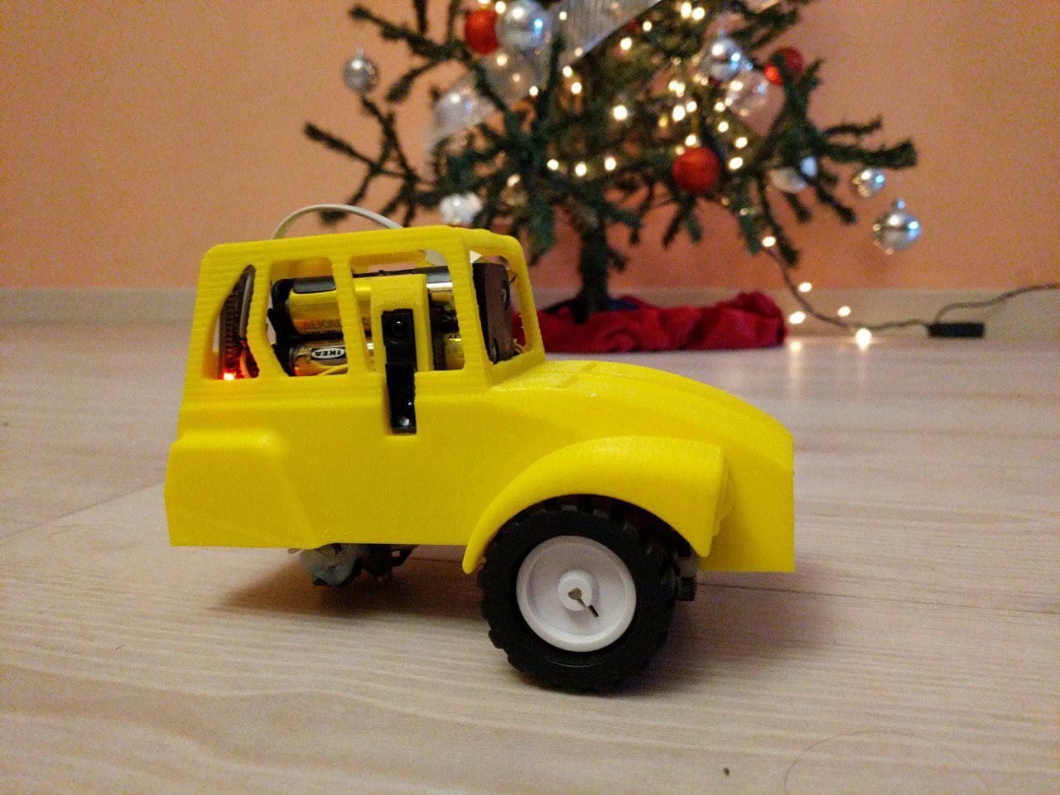
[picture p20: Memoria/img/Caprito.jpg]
  
  \caption{Imagen del robot con su chásis}
  \label{A}
\end{figure}

Se muestra además, una pequeña galería del robot en general:

\begin{figure}[h!]
\centering
\begin{tabular}{ccc}
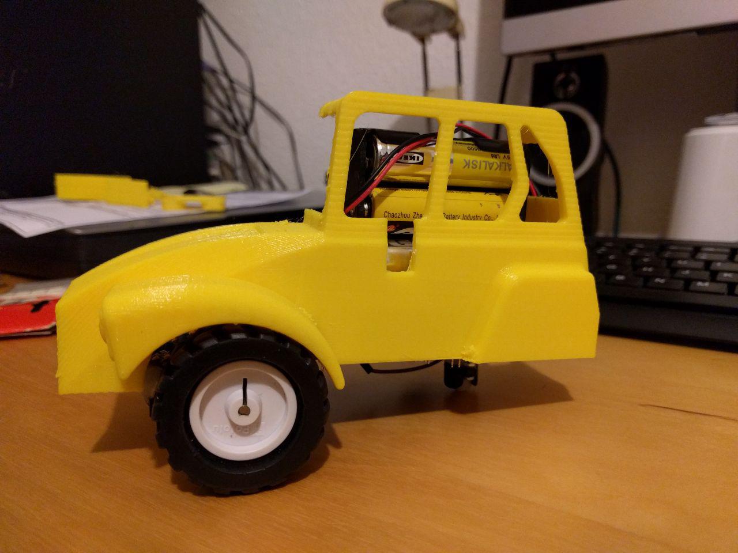
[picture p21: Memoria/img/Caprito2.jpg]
  
&
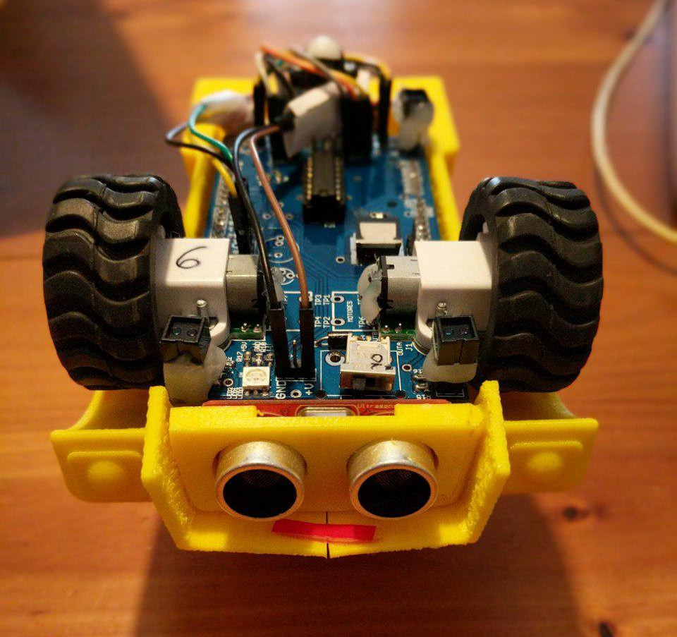
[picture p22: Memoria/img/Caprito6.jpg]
  
  &
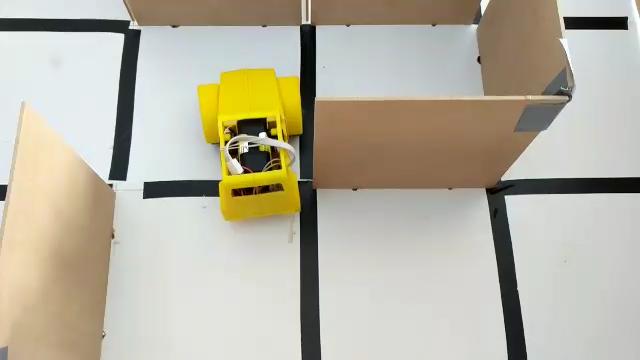
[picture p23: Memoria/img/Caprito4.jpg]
  \\
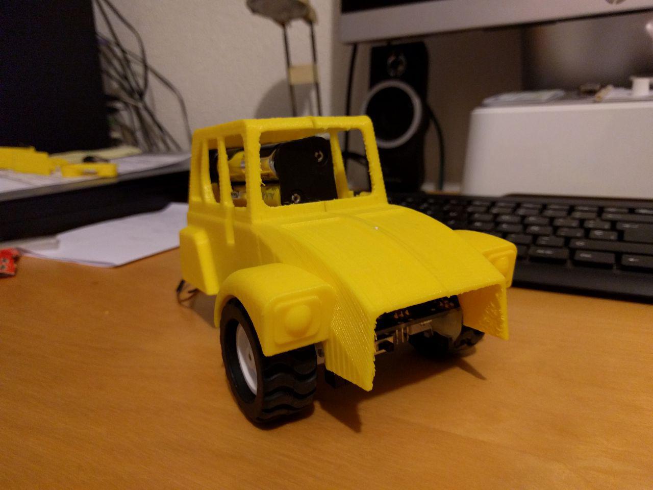
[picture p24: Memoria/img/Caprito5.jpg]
  
  &
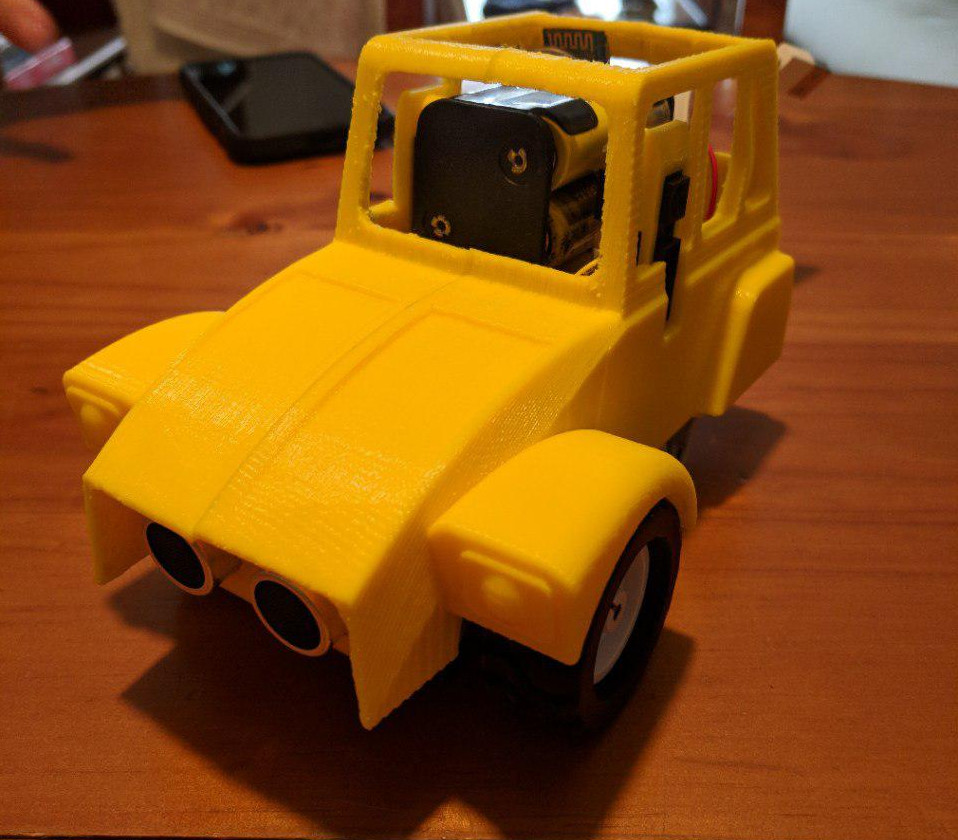
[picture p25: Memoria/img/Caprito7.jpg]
  
  &
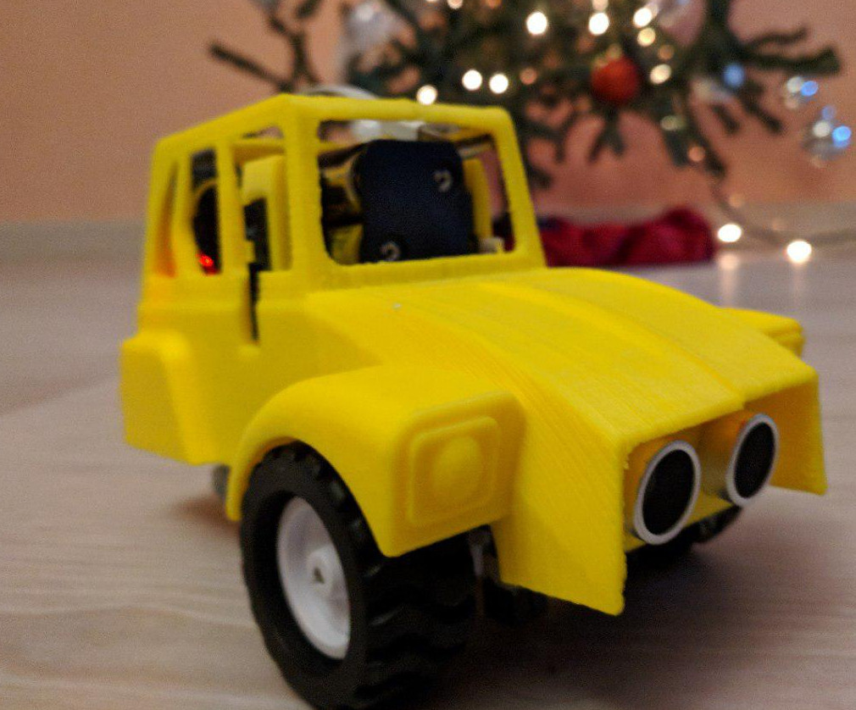
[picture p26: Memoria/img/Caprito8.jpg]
  \\

\end{tabular}
\caption{Galería del robot}
\end{figure}

\newpage
Finalmente se incluyen algunas capturas de la aplicación móvil desarrollada:

\begin{figure}[h!]
\centering
\begin{tabular}{ccc}
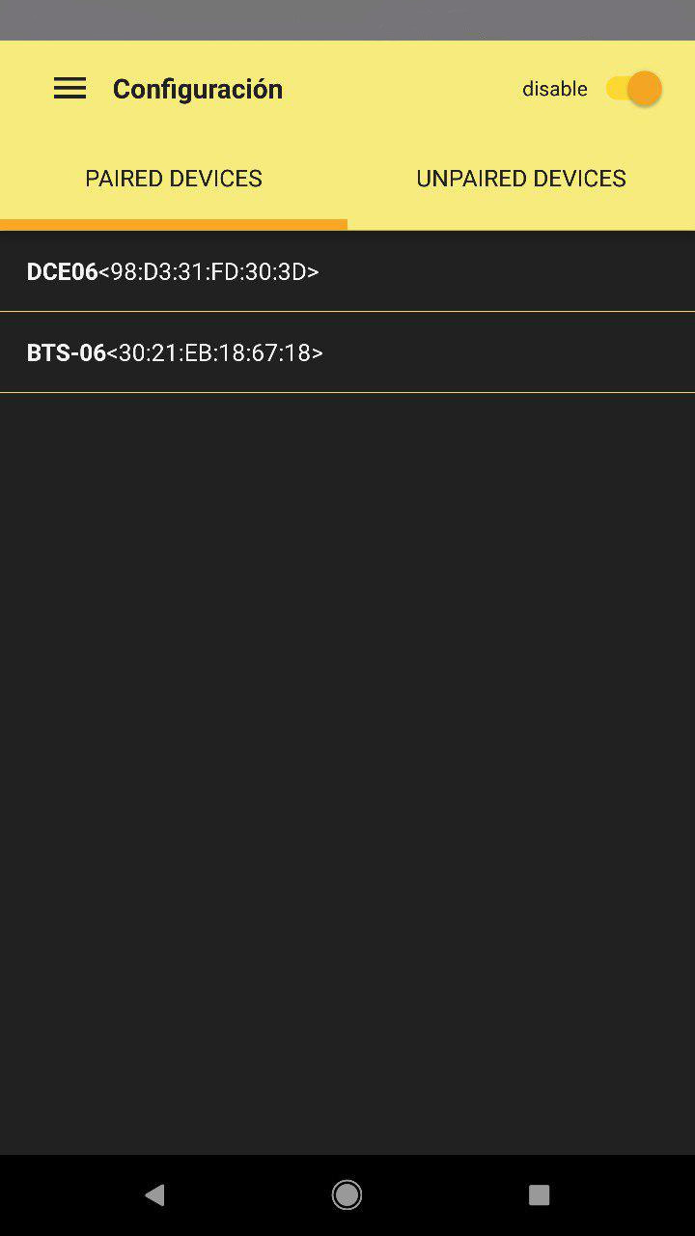
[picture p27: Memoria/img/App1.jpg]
  
&
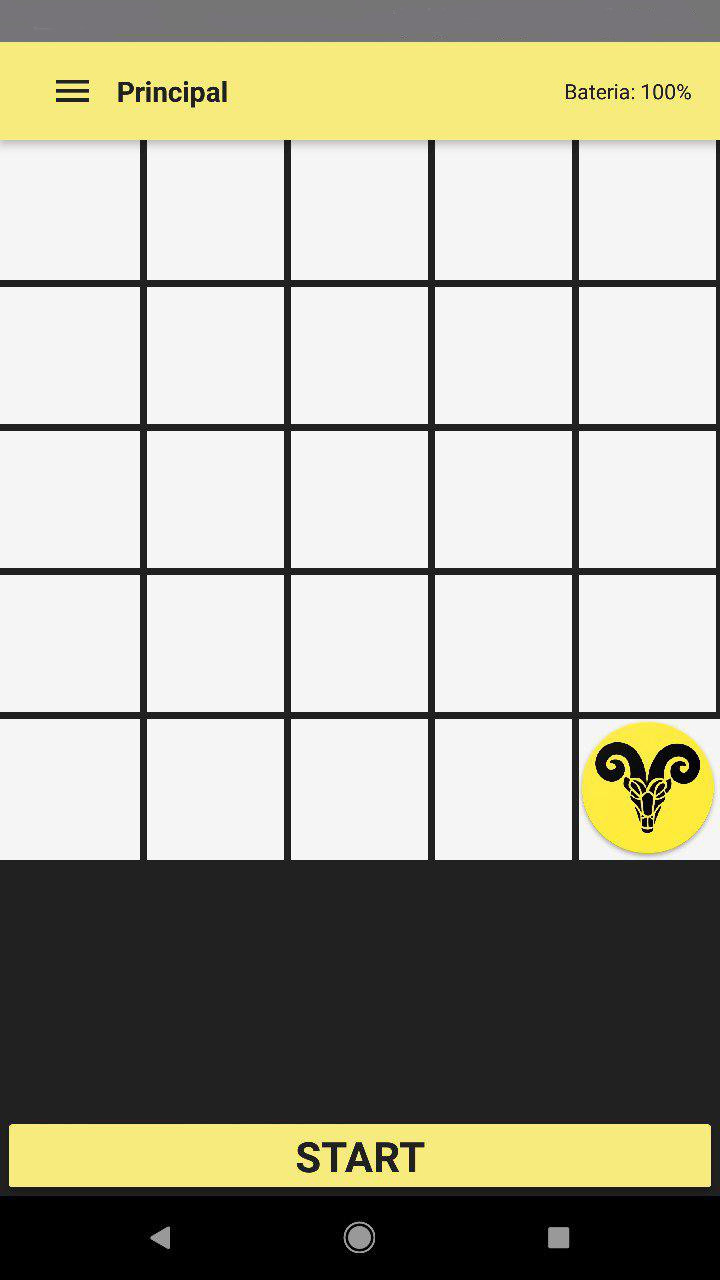
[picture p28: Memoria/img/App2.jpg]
  
&
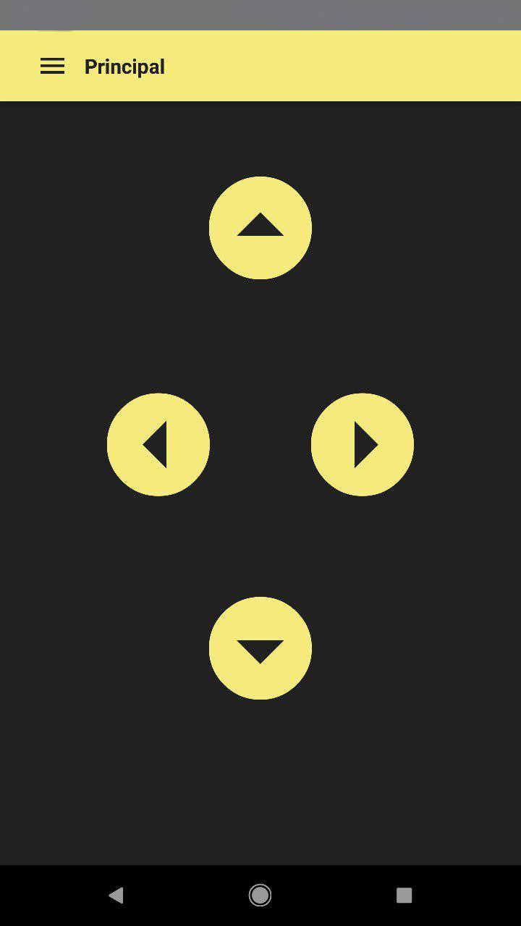
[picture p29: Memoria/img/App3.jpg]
  \\
\end{tabular}
\caption{Muestra de la aplicación móvil}
\end{figure}

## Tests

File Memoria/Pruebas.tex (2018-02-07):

\chapter{PRUEBAS}

\begin{table}[h!]
  \centering
  \begin{adjustbox}{max width=\textwidth}
  \begin{tabular}{|c|c|c|}
    \hline
    ID & CATEGORÍA & COMPROBACIÓN \\ \hline
    \rowcolor{gray!20}

    RF01 & Movimiento & \checkmark El robot se mueve gracias al uso de los encoders. \\ \hline
    \rowcolor{gray!20}

    RF02 & Movimiento & \checkmark El robot es capaz de girar 90º a la derecha con uso de encoders. \\ \hline
    \rowcolor{gray!20}

    RF03 & Movimiento & \checkmark El robot es capaz de girar 90º a la izquierda con el uso de encoders. \\ \hline
    \rowcolor{gray!20}

    RF04 & Movimiento & \checkmark El robot al no detectar una pared frontal, es capaz de moverse en línea recta. \\ \hline
    \rowcolor{gray!20}

    RF05 & Movimiento & \checkmark Al cumplirse el requisito anterior, se cumple este. \\ \hline
    \rowcolor{red!20}

    RF06 & Detección &  \checkmark Gracias al uso de ultrasonidos, se detecta la existencia de paredes frontales.  \\ \hline
    \rowcolor{red!20}

    RF07 & Detección & \checkmark Gracias al uso del Sharp derecho, se detecta la existencia de paredes a la derecha.  \\ \hline
    \rowcolor{red!20}

    RF08 & Detección & \checkmark Gracias al uso del Sharp izquierdo, se detecta la existencia de paredes a la derecha. \\ \hline
    \rowcolor{red!20}

    RF09 & Detección  & \checkmark Gracias al uso de los CNY70 se detecta la transición entre celdas. \\ \hline
    \rowcolor{red!20}

    RF10 & Detección & \checkmark Gracias al uso de los CNY70 se detecta la casilla de salida. \\ \hline
    \rowcolor{red!20}

    RF11 & Resolución & \checkmark Se almacena información sobre las celdas ya visitadas.  \\ \hline
    \rowcolor{yellow!40}

    RF12 & Resolución & \checkmark Debido al RF anterior, se decide cuáles son los posibles movimientos a realizar. \\ \hline
    \rowcolor{yellow!40}

    RF13 & Resolución & \checkmark El robot es capaz de recorrer varias celdas gracias al algoritmo implementado.  \\ \hline
    \rowcolor{yellow!40}

    RF14 & Resolución & \checkmark El robot es capaz de resolver el laberinto. \\ \hline
    \rowcolor{green!20}

    RF15 & Información & \checkmark Se manda información a la app sobre las celdas recorridas. \\ \hline

    \rowcolor{green!20}

    RF16 & Información & \checkmark Se manda información a la app sobre sobre los obstáculos que hay en cada celda. \\ \hline

    \rowcolor{green!20}

    RF17 & Información & \checkmark Se manda información a la app sobre la velocidad que lleva el robot. \\ \hline

    \rowcolor{green!20}

    RF18 & Información & \checkmark Se manda información a la app sobre la distancia que ha recorrido el robot.  \\ \hline

    \rowcolor{green!20}

    RF19 & Información & \checkmark Se manda información a la app sobre el tiempo que lleva el robot en el laberinto.  \\ \hline

    \rowcolor{green!20}

    RF20 & Información & \checkmark Se manda información sobre la trayectoria realizada por el robot.  \\ \hline

    \rowcolor{green!20}

    RF21 & Información & \checkmark Se manda información sobre el nº de celdas recorridas. \\ \hline

    \rowcolor{green!20}

    RF22 & Información & \checkmark La aplicación muestra el estado del laberinto, tal y como se muestra en la figura 8.4 \\ \hline
    \rowcolor{orange!40}

    RF23 & Usuario & \checkmark El usuario dispone de una aplicación móvil en la que puede comprobar multitud de cosas \\ \hline

    \rowcolor{blue!20}

    RF24 & Pruebas & \checkmark Se dispone de una batería de pruebas que comprueba el correcto funcionamiento de todos los sensores \\ \hline

  \end{tabular}
\end{adjustbox}
  \caption{Requisitos Funcionales}
  \label{ReqFuncionalesPruebas}

\end{table}

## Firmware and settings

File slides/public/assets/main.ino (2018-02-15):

#include <StandardCplusplus.h>
#include <stack>
#include "Timer.h"
#include "Robot.hpp"

const int RIGHT = 1;
const int FORWARD = 2;
const int LEFT = 4;
const int BACKWARD = 8;
const int LEFT_BACKWARD = 16;
const int RIGHT_BACKWARD = 32;

Timer t;

int lastMovement = 7;
std::stack<int> Movements;
std::stack<int> PrintMov;

int CNY[] = {A0,A1,A5}; // CNYLeft, CNYRight, CNYBottom
int Sharp[] = {A8,A4}; // SHarpLeft, SharpRight
int Ultrasonic[] = {A3,11};
int MotorR[] = {5,6};
int MotorL[] = {9,10};
int Led[] = {12,13,11}; // Led1, Led2, Led3
int Battery = A6;

Robot::tState State = Robot::waiting; // Must start in waiting

Robot robot(CNY,Sharp,Ultrasonic,MotorL,MotorR,Led,Battery,State,3,2);

void handle_battery(){
  //Serial1.print("bt" + String(pos[0]) + String(pos[1])+"#");
  //Serial1.print("bt" + String(robot.BatteryState(),2) + "#");
}

void setup() {
  Serial1.begin(9600); // Bluetooth
  Serial.begin(9600);
  robot.init();
  int tickEvent = t.every(500, handle_battery);
}

void loop() {
  //delay(1500);
  String btread = robot.ReadBT();

  if(btread == "start"){State = Robot::lookingforEXIT;}
  switch (State) {
    case Robot::waiting:
      break;

    case Robot::lookingforEXIT:
      lookforEXIT();
      break;

    case Robot::lookingforSTART:
      lookforSTART();
    break;
  }/*
  delay(3000);
  testSensors();*/
}

void lookforEXIT() {
  Serial1.print("music1#");
  int ini, fin;
  while (!isTheEnd()) {
    Serial1.print("bt" + String(robot.BatteryState(),2) + "#");

    int allowedMovement = checkWalls();
    testSensors();
    if (allowedMovement & RIGHT & lastMovement) {
      Serial1.print("0#");
      //testSensors();
      ini = robot.ReadSharp('R');
      Movements.push(RIGHT);
      robot.Move(Robot::right,200);
      robot.Move(Robot::forward,200);
      robot.Move(Robot::stoprobot,0);
      fin = robot.ReadUltrasonic();
      Serial1.print("dist" + String(fin-ini) + "#");
      Serial.println(fin-ini);
      Serial1.print("casilla#");
      lastMovement = 7; delay(3000);
    } else {
      if (allowedMovement & FORWARD & lastMovement) {
        Serial1.print("1#");
        //testSensors();
        ini = robot.ReadUltrasonic();
        Movements.push(FORWARD);
        robot.Move(Robot::forward,200);
        robot.Move(Robot::stoprobot,0);
        fin = robot.ReadUltrasonic();
        Serial1.print("dist" + String(fin-ini) + "#");
        Serial1.print("casilla#");
        lastMovement = 7; delay(3000);
       

      } else {
        if (allowedMovement & LEFT & lastMovement) {
          Serial1.print("2#");      
          //testSensors();
          ini = robot.ReadSharp('R');
          Movements.push(LEFT);
          robot.Move(Robot::left,200);
          robot.Move(Robot::forward,200);
          robot.Move(Robot::stoprobot,0);
          fin = robot.ReadUltrasonic();
          Serial1.print("dist" + String(fin-ini) + "#");
          Serial1.print("casilla#");
          lastMovement = 7; delay(3000);
        } else {
          if (!Movements.empty()) {
            if (Movements.top() & FORWARD) {
              Serial1.print("3#");
              //testSensors();
              ini = robot.ReadUltrasonic();
              Movements.pop();
              robot.Move(Robot::backward,200);
              robot.Move(Robot::stoprobot,0);
              fin = robot.ReadUltrasonic();
              Serial1.print("dist" + String(fin-ini) + "#");
              lastMovement = 4; delay(3000);
            } else {
              if (Movements.top() & RIGHT) {
                Serial1.print("5#");   
                //testSensors();
                ini = robot.ReadUltrasonic();
                Movements.pop();
                robot.Move(Robot::backward,200);
                robot.Move(Robot::rightbackward,200);
                robot.MoveEncoder(Robot::E_forward,200,200,3);
                fin = robot.ReadSharp('R');
                Serial1.print("dist" + String(fin-ini) + "#");
                robot.Move(Robot::stoprobot,0);
                lastMovement = 6; delay(3000);
              } else { // LEFT
                Serial1.print("4#");
                //testSensors();
                ini = robot.ReadUltrasonic();
                Movements.pop();
                robot.Move(Robot::backward,200);
                robot.Move(Robot::leftbackward,200);
                robot.MoveEncoder(Robot::E_forward,200,200,3);
                fin = robot.ReadSharp('L');
                Serial1.print("dist" + String(fin-ini) + "#");
                robot.Move(Robot::stoprobot,0);
                lastMovement = 0; delay(3000);
              }
            }
          }
        }
      }
    }
  }
  robot.Move(Robot::stoprobot,0);
  Serial1.print("congrats#");
  for(int i=0; i<10; i++){
    if(i%2==0){
      robot.TurnOnLed('R',254); 
      robot.TurnOnLed('G',0);
    }
    else{
      robot.TurnOnLed('G',254);
      robot.TurnOnLed('R',0);
    }
    delay(500);
  }
  robot.TurnOnLed('D',0);
  delay(50);
  State = Robot::lookingforSTART;
}

void lookforSTART() {
  int mov;
  Serial1.print("music2#");
  int ini, fin;
  while(!Movements.empty()){
     mov = robot.ReverseMov(Movements.top());
     switch(mov){
        case RIGHT_BACKWARD:
           ini = robot.ReadUltrasonic();
           robot.Move(Robot::backward,200);
           robot.Move(Robot::rightbackward,200);
           robot.MoveEncoder(Robot::E_forward,200,200,3);         
           fin = robot.ReadSharp('R');
           Serial1.print("dist" + String(fin-ini) + "#");
           Serial1.print("5#");
           robot.Move(Robot::stoprobot,0);
           delay(3000);
          break;
        case LEFT_BACKWARD:
           ini = robot.ReadUltrasonic();
           robot.Move(Robot::backward,200);
           robot.Move(Robot::leftbackward,200);
           robot.MoveEncoder(Robot::E_forward,200,200,3);
           fin = robot.ReadSharp('L');
           Serial1.print("dist" + String(fin-ini) + "#");
           Serial1.print("4#");
           robot.Move(Robot::stoprobot,0);
           delay(3000);
          break;
        case BACKWARD:
           ini = robot.ReadUltrasonic();
           robot.Move(Robot::backward,200);
           fin = robot.ReadUltrasonic();
           Serial1.print("dist" + String(fin-ini) + "#");
           Serial1.print("3#");
           robot.Move(Robot::stoprobot,0);
           delay(3000);
          break;

        default:
          break;
     }
     Movements.pop();
  }
 // Serial1.print("fin");
}

int checkWalls() {
  int result = 0;
  if (13 < robot.ReadSharp('L') || robot.ReadSharp('L') < 0) {
    result |= LEFT;
  }
  if (13 < robot.ReadSharp('R') || robot.ReadSharp('R') < 0) {
    result |= RIGHT;
  }
  if (10 < robot.ReadUltrasonic()) {
    result |= FORWARD;
  }
  return result;
}

void radioControl(String m) {
   robot.Encoder(false);
   //if (Serial1.available() > 0 ) {
     //String m = robot.ReadBT();
     robot.MoveAbsolute(m[0],150,150);
   //}
}

bool isTheEnd() { // All CNY are Black
  return robot.ReadCNY('L')&&robot.ReadCNY('R')&&robot.ReadCNY('B');
}

void testSensors() {
  /*Serial1.print("Battery: "); Serial1.println(String(robot.BatteryState(),2));
  if (robot.ReadCNY('L'))
    Serial1.println("CNY L Black");
  else Serial1.println("CNY L White");
  if (robot.ReadCNY('R'))
    Serial1.println("CNY R Black");
  else Serial1.println("CNY R White");
  if (robot.ReadCNY('B'))
    Serial1.println("CNY B Black");
  else Serial1.println("CNY B White");
  Serial1.print("Ultrasonic: "); Serial1.println(robot.ReadUltrasonic());
  Serial1.print("Sharp L: "); Serial1.println(robot.ReadSharp('L'));
  Serial1.print("Sharp R: "); Serial1.println(robot.ReadSharp('R'));
  /*Serial1.println("~~~~~~~~~~~~~~~~~~~~");
  Serial1.print("Stack: "); 
  while(!Movements.empty()){
    Serial1.print(Movements.top()); Serial1.print(", ");
    PrintMov.push(Movements.top());
    Movements.pop();
  }
  
  while(!PrintMov.empty()){
    Movements.push(PrintMov.top());
    PrintMov.pop();
  }
  */
}

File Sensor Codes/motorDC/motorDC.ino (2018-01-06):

/* Giro alterno de motor DC con driver L293D */

//Definición de variables
const int in1PinRight = 9; // Right motor
const int in2PinRight = 10;
const int in1PinLeft = 5; // Left motor
const int in2PinLeft = 6;
int Speed_Value = 100;
const float disminucion = 0.95;

void setup() {
    pinMode(in1PinRight, OUTPUT);
    pinMode(in2PinRight, OUTPUT);
    pinMode(in1PinLeft, OUTPUT);
    pinMode(in2PinLeft, OUTPUT);
}

void loop() {
  Speed_Value=100;
    if (Speed_Value<=500) {
        int sp_v = map(Speed_Value,500,0,0,255);
        forwardMotor(sp_v);
    }else {
        if((500<Speed_Value)&&(Speed_Value<520))
            stopMotor();
        else{
            int sp_v = map(Speed_Value,520,1023,0,255);
            reverseMotor(sp_v);
        }
    }
  delay(3000);
  stopMotor();

  delay(1000);

  // Giro Derecha y Giro Izquiera
  Speed_Value=100;
  delay(1000);
  if (Speed_Value<=500) {
        int sp_v = map(Speed_Value,500,0,0,255);
        left(sp_v);
    }else {
        if((500<Speed_Value)&&(Speed_Value<520))
            stopMotor();
        else{
            int sp_v = map(Speed_Value,520,1023,0,255);
            right(sp_v);
        }
    }
  delay(1000);

  stopMotor();

  delay(1000);
}

void reverseMotor (int speed_Value) {
    analogWrite(in1PinRight,speed_Value);
    analogWrite(in2PinRight,LOW);
    analogWrite(in1PinLeft,speed_Value*disminucion);
    analogWrite(in2PinLeft,LOW);
}

void forwardMotor (int speed_Value) {
    analogWrite(in1PinRight,LOW);
    analogWrite(in2PinRight,speed_Value);
    analogWrite(in1PinLeft,LOW);
    analogWrite(in2PinLeft,speed_Value*disminucion);
}

void left (int speed_Value) {
    analogWrite(in1PinRight,speed_Value);
    analogWrite(in2PinRight,LOW);
    analogWrite(in1PinLeft,LOW);
    analogWrite(in2PinLeft,speed_Value*disminucion);
}

void right (int speed_Value) {
    analogWrite(in1PinRight,LOW);
    analogWrite(in2PinRight,speed_Value);
    analogWrite(in1PinLeft,speed_Value*disminucion);
    analogWrite(in2PinLeft,LOW);
}

void stopMotor() {
    analogWrite(in1PinRight,LOW);
    analogWrite(in2PinRight,LOW);
    analogWrite(in1PinLeft,LOW);
    analogWrite(in2PinLeft,LOW);
}

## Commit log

2017-11-24 Sensor codes
2017-12-01 New sensor codes
2017-12-27 App with serial communication between android and arduino
2018-01-02 3D Model
    [MitadCocheParte1.stl, MitadCocheParte2.stl, Sharp1.stl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]
2018-01-02 Sharp model
    [Sharp.stl]
2018-01-02 Removed extra sharp
    [Sharp1.stl, Sharp2.stl]
2018-01-06 3D model fixed
    [MitadCocheParte1.stl, MitadCocheParte2.stl, Ultrasonic.stl]
2018-01-06 Sensor updated
2018-01-18 Robot library with main arduino program
2018-01-18 Show battery status
2018-01-19 Added send battery status each 500ms
2018-01-19 Wheel encoder
2018-01-19 Encoder in Robot library
2018-02-02 Used STL on arduino
2018-02-08 New Ultrasonic
